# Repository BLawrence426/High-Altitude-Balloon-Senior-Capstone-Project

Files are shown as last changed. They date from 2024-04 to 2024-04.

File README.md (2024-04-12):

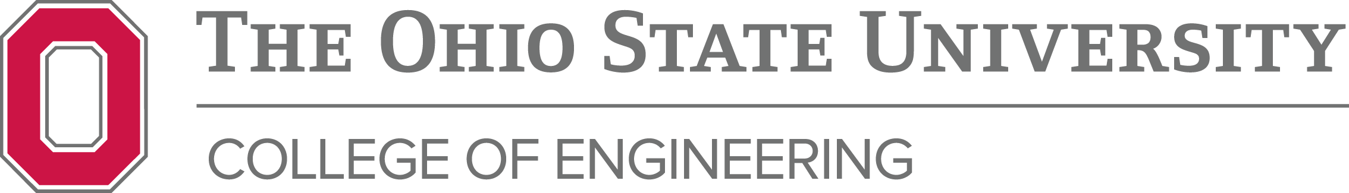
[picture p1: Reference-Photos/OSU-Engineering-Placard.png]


# High Altitude Balloon (HAB) Senior Capstone Project

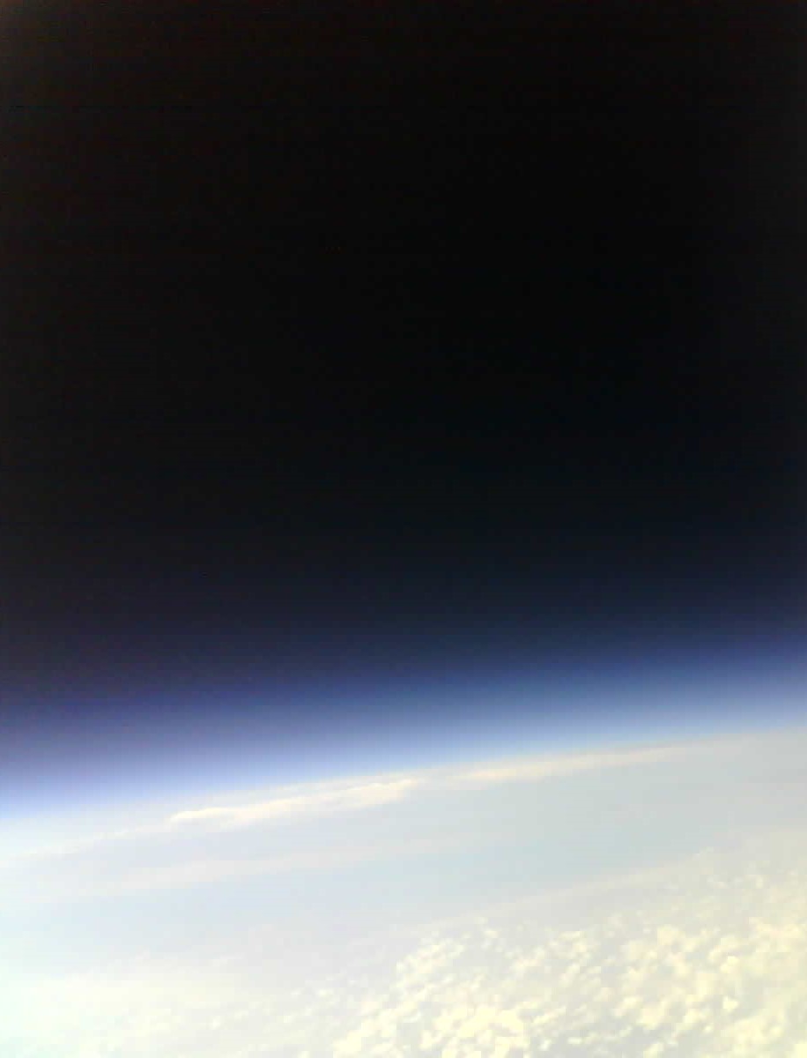
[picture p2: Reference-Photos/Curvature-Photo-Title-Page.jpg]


## Contents
1. [Project Importance](#user-content-project-importance)
2. [Every Parts List](#user-content-every-parts-list)
3. [Payload Construction](#user-content-payload-construction)
4. [Payload Arduino Code](#user-content-payload-arduino-code)
5. [Tracking Receiver Construction](#user-content-tracking-receiver-construction)
6. [Tracking Receiver Arduino and MATLAB Code](#user-content-tracking-receiver-arduino-and-matlab-code)
7. [Launch Protocol](#user-content-launch-protocol)
8. [Launch Experience and Data Results](#user-content-launch-experience-and-data-results)
9. [Flight Test Data Comparison to Simulation Code](#user-content-flight-test-data-comparison-to-simulation-code)
10. [Photo Results](#user-content-photo-results)
11. [Suggestions for Improvements](#user-content-suggestions-for-improvements)
12. [Final Thoughts and Reflection](#user-content-final-thoughts-and-reflection)
13. [Useful Online Tools](#user-content-useful-online-tools)
14. [Resources and Inspirations](#user-content-resources-and-inspirations)
15. [Acknowledgements](#user-content-acknowledgements)

## Project Importance
For my senior year of college at The Ohio State University, we were assigned a capstone group tasked with completing a year-long project. There were a variety of topics we could possibly be assigned; from creating a workbench meant for Starlab to conducting research for both the Navy and Airforce to creating a cost-effective high-altitude balloon (HAB) using off-the-shelf components. Can you guess which one I was assigned?

For more context on the reason behind this project, the first aerospace engineering course (AERO 2200: Introduction to Aerospace Engineering) that each new, bright-eyed sophmore in the major takes will conduct a high-altitude balloon lab at one point. This lab involves a launch of a high-altitude balloon by the professor and other academic faculty in order to collect atmospheric data such as ambient temperature and pressure in order to be analyzed by the students. The purpose for this lab is to teach the students the standard atmosphere (specifically, how air pressure, temperature, and density changes with altitude).

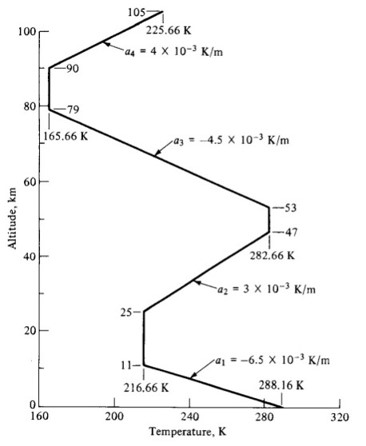
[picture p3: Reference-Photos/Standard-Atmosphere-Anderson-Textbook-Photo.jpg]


#### (Figure from Introduction to Flight Ninth edition by J.D. Anderson, Jr. and M.L. Bowden)

In prior years, including my sophmore year, there were a multitude of issues with the commerical weather balloons that can be bought off the internet (i.e., QRP Light Tracker and Tracksoar). The issues ranging from the balloons themself pre-maturely bursting before it could reach the target altitude or the payload electronics being lost mid-flight. This was a concern to the Mechanical and Aerospace Engineering (MAE) Department since each year they would have to spend upwards of $1000+ for a new weather balloon. This is where our project's importance came in since the goal was to create a new weather balloon payload using off-the-shelf components that was cost-effective (sub $600 for the payload) that could reliably reach a target altitude of 100,000 ft and be recovered for future use. If it couldn't be recovered, the low cost for each payload was important so the department wouldn't need to spend as much money for each launch.

## Every Parts List

### Electronics Parts List

|Hardware|Description|Price|Amount|Total Cost|
| --- | --- | --- | --- | --- |
| [Arduino MKR WAN 1310](https://store-usa.arduino.cc/products/arduino-mkr-wan-1310?selectedStore=us) | The Microcontroller that ran all the payload sensors. Also has built-in Long Range (LoRa) Wide-Area-Network (WAN) module. | $46.00 | 2 | $92.00 |
| [Arduino GPS Shield](https://store-usa.arduino.cc/products/arduino-mkr-gps-shield) | Arduino's own GPS board that can be easily attached to Arduino MKR WAN 1310 board. | $40.10 | 1 | $40.10 |
| [DS18B20 Waterproof Temp. Sensors](https://www.amazon.com/dp/B08V93CTM2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) | Waterproof temperature sensors capable of recording down -55℃. Preferably want two: one for atmospheric temp. and the other for payload internal temp. | $13.48 | 1 | $13.48 |
| [Adafruit MPRLS Ported Pressure Sensor](https://www.adafruit.com/product/3965) | Pressure sensor capable of reading down to 0 psi. Ported end allows for silicone tube to be connected and allow pressure sensor to remain inside the payload | $29.95 | 1 | $29.95 |
| [Adafruit PCF8523 Real Time Clock (RTC) Board](https://www.adafruit.com/product/3295) | Keeps date and time. This helps timestamp each data set for easier analysis of data later. You would think a $40+ Arduino board could do this on its own but NOPE! | $6.95 | 1 | $6.95 |
| [3.7v 3700mAh Lithium Polymer Battery](https://www.amazon.com/EEMB-3700mAh-Rechargeable-Connector-Certified/dp/B08215B4KK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) | Power supply for the entire payload. This may be overkill and can easily be substituted for different capacity battery | $16.99 | 1 | $16.99 |
| [ESP32-CAM Board w/ OV2640 2MP Camera Module](https://www.amazon.com/ESP32-CAM-MB-Aideepen-ESP32-CAM-Bluetooth-Arduino/dp/B0948ZFTQZ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) | On-board camera meant to take photoes every 30 seconds and store to an on-board micro-SD card. This can be omitted if pictures aren't desired | $19.99 | 1 | $19.99 |
| [5mm Micro Mini Slide Switch (3 pin/2 position)](https://www.amazon.com/Tnuocke-Vertical-Position-Switches-SS12D10-G5/dp/B099N61GTZ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) | Turns on/off the payload. | $6.95 | 1 | $6.95 |
| [Micro-SD Card Breakout Board](https://www.amazon.com/Integrated-Circuit-Interface-Raspberry-Breakout/dp/B08C4WY2WR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) | For storing each packet of data on-board the payload iteself. This way if the radio packets end up corrupted or garbage this shouldn't be compromised. | $5.99 | 1 | $5.99 |
| [Wire](https://www.amazon.com/TUOFENG-Hookup-Wires-6-Different-Colored/dp/B07TX6BX47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) | For connecting everything together. I'm weird and I really like color coordinating all my wires so I don't blow anything up. Obviously can be omitted from parts if you already have some.  | $14.99 | 1 | $14.99 |
| [Solder](https://www.amazon.com/Rosin-Solder-Electrical-Soldering-JWOWO/dp/B0C7KZF11F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) | For connecting everything together. I highly, HIGHLY recommend soldering everything together. The jetstreams up above can get pretty nasty and really put your payload through the wringer. | $7.99 | 1 | $7.99 |
| [SUSB Type-C Charging Module](https://www.amazon.com/Charging-Lithium-Battery-Charger-Protection/dp/B08X6G26Q8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) | I noticed some issues with connecting the battery & switch directly to the battery connecter on the Arduino. So I attached one of these to the batteries to make sure it would be fully charged before the flight. | $7.99 | 1 | $7.99 |
| [0.96 Inch OLED Display](https://www.amazon.com/GeeekPi-SSD1306-Display-Arduino-Raspberry/dp/B0833PF7ML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) | Used on the tracking receiver to display the HAB's current latitude, longitude, and altitude. | $14.99 | 1 | $14.99 |
| [1.2" x 1.2" Perfboard](https://www.amazon.com/gp/product/B0CBPRBRTT/ref=ppx_yo_dt_b_search_asin_title?ie=UTF8&psc=1) | Used these to create "hubs" for the various wires. Like connecting all power, ground, SCL, and SDA pins together | $7.09 | 1 | $7.09 |

### Launch Equipment List

|Equipment|Description|Price|Amount|Total Cost|
| --- | --- | --- | --- | --- |
| [Helium](https://www.ballooniacs.com/medium-110-cu-ft-helium-tank-rental/) | Obviously need helium for our balloon. Tank rentals can vary, but if you are in the Columbus, OH area I highly recommend BALLOONIACS. They are very nice and were able to get us a tank of helium on very short notice. Just make sure you double check how much helium you will need before launch! | ~$300.00 | 1 | ~$300.00 |
| [Balloon(s)](https://www.scientificsales.com/8244-Weather-Balloon-1200-Grams-Natural-p/8244.htm) | Obviously need a balloon so our project lifts of the ground. Just double check the size balloon you need to reach your target altitude. We went with a 1200 gram balloon in order to reach 100,000 ft | $110.00 | 1 | $110.00 |
| [Pressure Regulator](https://www.amazon.com/Harris-3000606-25GX-Regulator-500-580/dp/B005V0RAYI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) | A pressure regulator helps fill the balloon safely. This is similar to the one we used, I just recommend getting one with a flared end in order to screw directly into the helium bottle. Obviously this can be replace with a similar device/method that is cheaper or more accessible to you! I was just fortunate enough to borrow one from our engineering department | $141.07 | 1 | $141.07 |
| [Quick Disconnect Hose](https://www.amazon.com/Hromee-Compressor-Fittings-Industrial-Coupler/dp/B08V17V6WJ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) | Air compressor hose for connecting the helium bottle to our ball-valve nozzle that is used to fill the balloon (pictured below). Doesn't have to be this exact same one, I just suggest something similar to this one. | $19.99 | 1 | $19.99 |
| [Fish Scale](https://www.amazon.com/dp/B07JWGHC48?ref=ppx_yo2ov_dt_b_product_details&th=1) | You can use this to determine how much helium is in your balloon. This gives the buoyancy force and then you can figure out the volume of helium inside the balloon if you assume it's spherical. I suggest making sure the fish scale can read the intended buoyancy force. | $19.99 | 1 | $19.99 |
| [Teflon Tape](https://www.menards.com/main/plumbing/plumbing-installation-repair/pipe-sealants-caulk-putty/blue-monster-teflon-pipe-thread-sealant-tape/70886/p-1444440440571-c-853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) | For sealing the threads of the pressure regulator when screwing it into the helium bottle | $4.31 | 1 | $4.31 |
| [Large Zip Ties](https://www.walmart.com/ip/Hyper-Tough-14-5-inch-75lb-Yellow-Cable-Ties-50-Count/595201774?from=/search) | For sealing the balloon and attaching the payload/parachute to the balloon. I recommend wrapping the part of the zip tie that will rub up against the balloon with a bit of electrical tape in order to prevent it from cutting the latex | $7.48 | 1 | $7.48 |
| [Wrenches](https://www.menards.com/main/tools/hand-tools/pliers-plier-sets/masterforce-reg-groove-joint-pliers/84-550/p-1444425505984-c-9156.htm) | For screwing the pressure regulator into the helium bottle. Just make sure whichever ones you use will fit the nut on the pressure regulator you're using | $9.78 | 1 | $19.78 |
| [Tarp](https://www.walmart.com/ip/Hyper-Tough-Weather-Resistant-Light-Duty-6-x-8-Polyethylene-Tarp/603949195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) | For setting up the balloon. Un-rolling the balloon in the grass can cause issues with the latex so I highly recommend getting a big tarp to set everything up | $4.66 | 1 | $4.66 |
| [Ball-Valve Filling Apparatus](https://www.highaltitudescience.com/products/3-cm-max-safe-inflator) | Mentioned previously, this was inserted into the neck of the balloon in order to fill it. A picture of it is included directly below. I HIGHLY reccommend you making your own. A hundred dollars for this one seems a bit extreme in my opinion and you could definitely make one for cheaper. | $99.99 | 1 | $99.99 |

### Personal Protective Equipment (PPE) List
|Equipment|Description|Price|Amount|Total Cost|
| --- | --- | --- | --- | --- |
| [Safety Glasses](https://www.amazon.com/dp/B016KZ2APQ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) | Want to be safe and protect your eyes! | $18.16 | 1 | $18.16 |
| [Vinyl Gloves](https://www.amazon.com/Schneider-Latex-Free-Powder-Free-Disposable-Examination/dp/B09KRSXZNL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) | The oils in your hands can cause week spots to form in the weather balloon so you really want to wear gloves when handling it. Just make sure they fit your hand size! | $7.57 | 1 | $7.57 |

### Payload Equipment List
|Equipment|Description|Price|Amount|Total Cost|
| --- | --- | --- | --- | --- |
| [Payload Chassis](https://www.amazon.com/HATCHBOX-3D-Filament-Dimensional-Accuracy/dp/B00J0ECR5I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) | Of my own design. It used a little under half a spool of PLA filament. I linked my preferred filament brand but use what ever your heart desires! | $24.99 | 1 | $24.99 |
| [1/2 Inch Syrofoam Insulation Board](https://www.homedepot.com/p/Owens-Corning-FOAMULAR-NGX-Insulating-Sheathing-0-5-in-x-4-ft-x-8-ft-SE-R-3-XPS-Rigid-Foam-Board-Insulation-13NGX/315193939) | Used this to make a shell to go on the outside of the chassis. This is to keep everything nice and toasty | $13.98 | 1 | $13.98 |
| [Aluminum Tape](https://www.amazon.com/Aluminum-Ductwork-Temperature-Insulation-Adhesive/dp/B0B6NDFXPN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) | Used this to assemble and seal the styrofoam shell. Doesn't need to be airtight nor should it be (though a very slim chance, could de-pressurize and explode). | $5.99 | 1 | $5.99 |
| [Bubble Wrap](https://www.walmart.com/ip/Duck-Max-Strength-Large-Bubble-Cushioning-Wrap-12-in-x-100-ft-Clear-287223/46582773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) | Wrapped the entire payload in bubble wrap for extra cushion upon impact. I was a bit worried about the impact velocity so I did this for ease of mind | $19.48 | 1 | $19.48 |
| [Plastic Paper Sheet Protector](https://www.walmart.com/ip/Pen-Gear-Economy-Sheet-Protectors-20-Sheets-Clear-8-5-x-11-Model-25038/935038091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) | This is for protecting the little placard I made with my contact information | $1.18 | 1 | $1.18 |
| [Packing Tape](https://www.walmart.com/ip/Scotch-Heavy-Duty-Shipping-Packing-Tape-Clear-1-88-in-x-25-6-yd-1-Tape-Roll-with-Dispenser/438482605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) | Used this for attaching the bubble wrap to the styrofoam shell | $3.58 | 1 | $3.58 |
| [Handwarmers](https://www.walmart.com/ip/HotHands-Hand-Warmer-10-Pair-Value-Pack/17808715?wl13=3792&selectedSellerId=0) | Heating source for the payload electronics | $7.48 | 1 | $7.48 |
| [Parachute](https://the-rocketman.com/recovery-html/) | Used for slowing down the payload upon the descent. I suggest weighing your payload and adding on the weight of the balloon youre using then going to the rocketman website to see what parachute size is suitable. I went with a 3ft parachute but I think we should have went up to either a 4ft or a 5ft parachute to slow it down even more. | $45.50 | 1 | $45.50 |
| [Paracord](https://www.walmart.com/ip/Hyper-Tough-550-Utility-Paracord-Rope-Orange-5-32-inch-x-50-feet/459593415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) | Used this for attaching the bubble wrap to the styrofoam shell | $4.84 | 1 | $4.84 |
| [Tape Measure](https://www.menards.com/main/tools/hand-tools/measuring-layout-tools/tape-measures-rulers/masterforce-reg-force-blade-trade-tape-measures/m52416/p-1460081133564-c-15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) | Used for measuring the length of the paracord between the payload/parachute/balloon | $7.09 | 1 | $7.09 |

### Miscellaneous Equipment List
|Equipment|Description|Price|Amount|Total Cost|
| --- | --- | --- | --- | --- |
| [Scissors](https://www.walmart.com/ip/Scotch-8-inch-Multi-Purpose-Stainless-Steel-Scissors/19675467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) | Used this for cutting bubble wrap and paracord | $3.62 | 1 | $3.62 |
| [Side Cutters](https://www.menards.com/main/tools/hand-tools/pliers-plier-sets/micro-flush-cutter/cwcmf/p-1444421187059-c-9156.htm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) | Used this for cutting paracord and zip ties | $3.55 | 1 | $3.55 |
| [Small Zip Ties](https://www.walmart.com/ip/Hyper-Tough-4inch-Cable-Tie-Uv-Black-100Pcs/440215826?athbdg=L1102&from=/search) | Used these for, albeit rough, cable management of thepayload electronics | $3.22 | 1 | $3.22 |
| [Electrical Tape](https://www.walmart.com/ip/Hyper-Tough-50ft-Vinyl-Electrical-Tape-3-4-0-43lbs-Black-3-Pack-34366/191038268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) | Used this for wire insulation and wrapping the PVC pipe used in the filling valve | $2.13 | 1 | $2.13 |
| [Lighter](https://www.walmart.com/ip/Ozark-Trail-Multipurpose-BBQ-Lighter-Red-and-Black-2-Pack/1450295214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) | Used for melting the cut ends of paracord so they don't keep fraying and coming loose | $2.24 | 1 | $2.24 |
| [Heat Shrink Tubing](https://www.amazon.com/Shrink-Tubing-Tubes-KOOWIN-Ratio/dp/B098LB9LTJ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) | The payload electronics are packed pretty tightly so I figured it would be best to insulate everything as neat as possible. This is the kit I used, but use whatever you feel like doing! | $7.99 | 1 | $7.99 |

## Payload Construction

When designing our HAB payload, the biggest fear that we needed to resolve was the absolute beating our payload electronics were expected to endure during a test flight. The jetstreams up above can get pretty nasty, so making sure that every component was a) soldered together and b) held down in some fashion was important to ensuring nothing would come loose and possibly short out the entire payload electronic system. Likewise, we wanted our payload to remain light (Under 2 pounds total, but preferably less) for safety reasons. So in conclusion, these three main considerations is what drove our design for what we are calling our payload chassis:

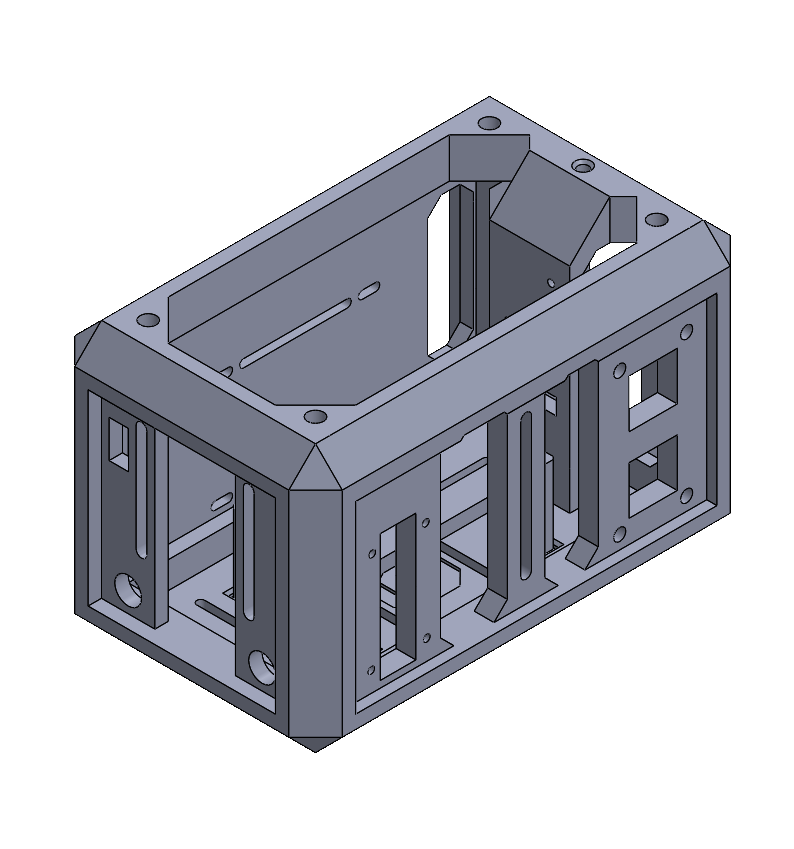
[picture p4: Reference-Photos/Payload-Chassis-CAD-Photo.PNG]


The chassis ended up having dimensions of 400x400x600mm (Base x Height x Width) and was 3D printed on my Ender 3 Pro printer using black hatchbox PLA. Chamfers were placed in as many locations as possible in order to cut-down on support material and decrease the printing time. Likewise, 10% infill was used but with 4 walls in order to help with strength and rigidity. This chassis is also divided up into two seperate pieces: the shell itself and a little platform with legs that was used for holding the Arduino MKR WAN 1310 board while still allowing for wires to pass underneath and be soldered to its pins. For more images of the chassis CAD files as well as the Solidworks files themself, go to the [Payload CAD Files](Payload-Chassis-CAD-Folder) folder up above!

Though its hard to see, I tried my best to remove as much unecessary material as possible while also providing ample mounting locations for each and every one of our electronics. The little holes seen all around our payload chassis are locations to melt threaded brass inserts into which provide locations that each part can be screwed down into. Similarly, I also tried putting a bunch of slots all around the chassis so zip ties could be passed through in order to hold everything into place. Our final designed had the Arduino MKR WAN 1310, micro-SD card board, RTC board, pressure sensor, and small perf boards screwed down and the wires, battery cell, antenna, and handwarmer zip tied to the chassis. The only odd methods out for mounting components onto our payload chassis were the ESP32-CAM board and the GPS shield. The GPS shield was insertted onto the top of the Arduino MKR WAN 1310 board and then hot-glued down to keep it from coming apart or shifting during flight. And then the camera was insertted into its own clam-shell case that was epoxied into a dedicated space on the chassis. This [clamshell case](https://www.thingiverse.com/thing:4251986) was designed by the username dandesc on Thingiverse.com and I decided to adapt it to work with our project. I belived this was a quicker way to provide a dedicated space for the camera to mount to while also making replacing it in the future if needed easy as well. And then once the chassis parts were printed, post-processed, and fully assembled I was left with this:

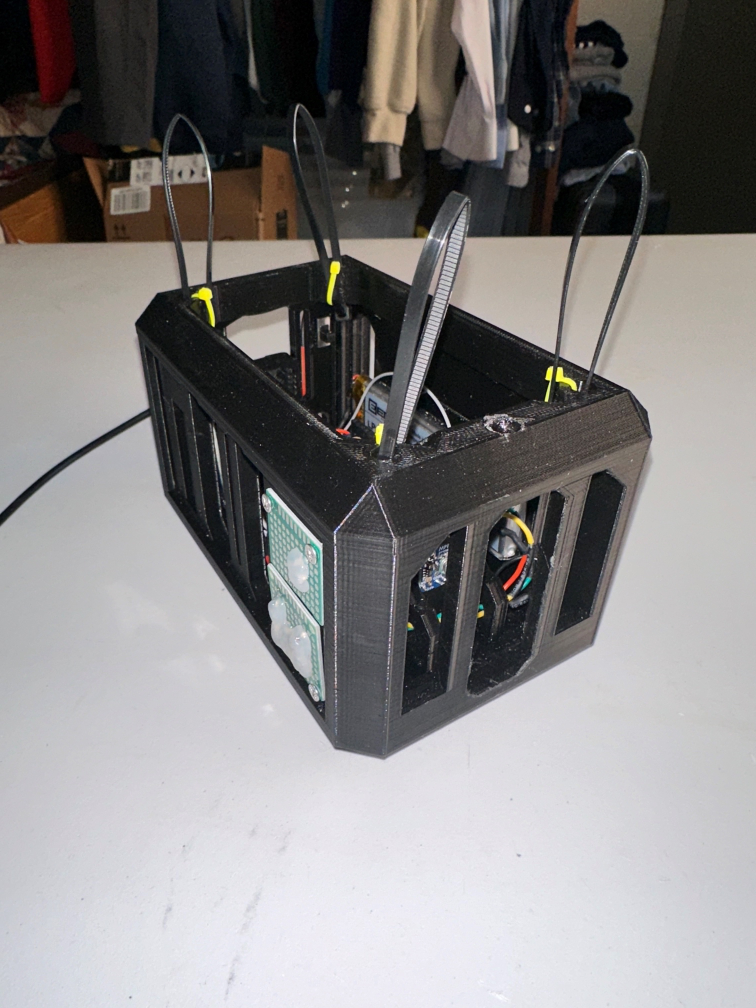
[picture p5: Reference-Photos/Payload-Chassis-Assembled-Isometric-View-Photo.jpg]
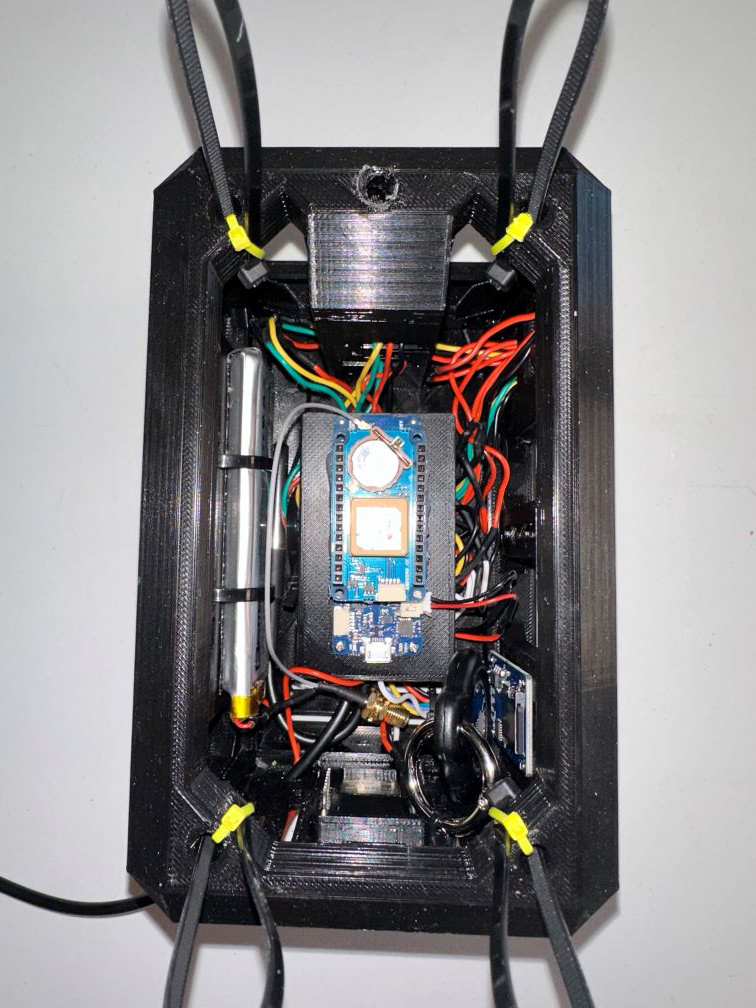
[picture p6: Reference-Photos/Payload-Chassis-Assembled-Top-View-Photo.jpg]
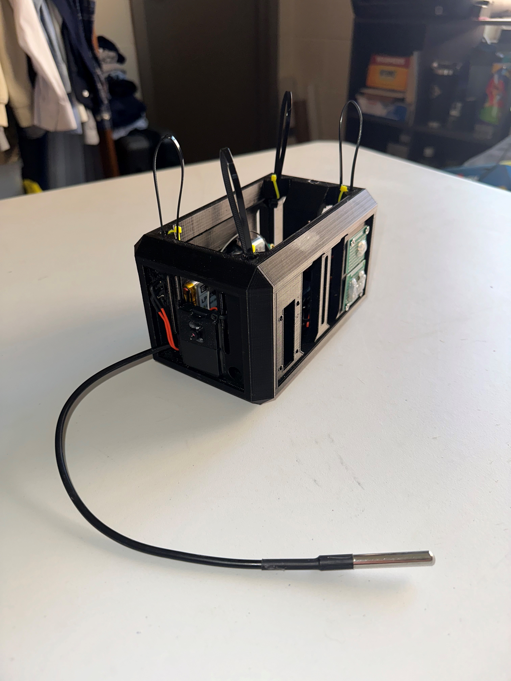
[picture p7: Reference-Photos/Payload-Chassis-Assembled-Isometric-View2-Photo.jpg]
  

My mindset for going this route instead of just saying screw it and epoxying all the components down was due to my desire to make each component easily replaceable if need be. I figure at some point a sensor or component will be damaged upon impact, so I figured I would try my best to future proof our mounting methods for each component. Plust it helped me with debugging things when I was assembling it all together and needed to address a weak connection to a component.

Likewise, when desinging our HAB payload, we did extensive online research and found a variety of individuals who posted their own HAB payload designs. The one design decision that was seen in all the ones we found was the use of an outer-styrofoam shell. These shells ranged from using small, disposable styrofoam coolers to even floral arrangement foam that was hallowed out. We decided to go a slightly different route and use 1/2 inch rigid foam insulation board and create an outer shell of this material that would go around our 3D printed chassis. A picture of our final styrofoam shell can be seen below:

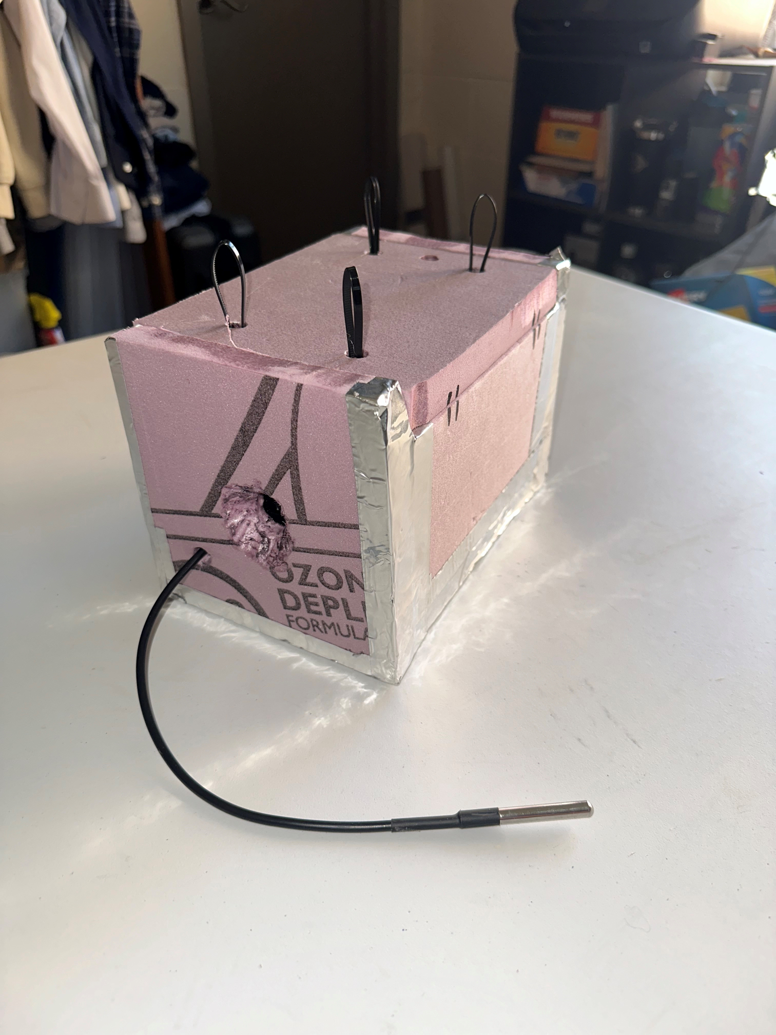
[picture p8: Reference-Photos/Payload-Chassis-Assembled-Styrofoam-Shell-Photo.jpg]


And then just to give us a bit more ease of mind with our payload, we decided to wrap it in several layers of bubble wrap in order to help cushion the impact force just incase our payload would happen to hit someone or their property.

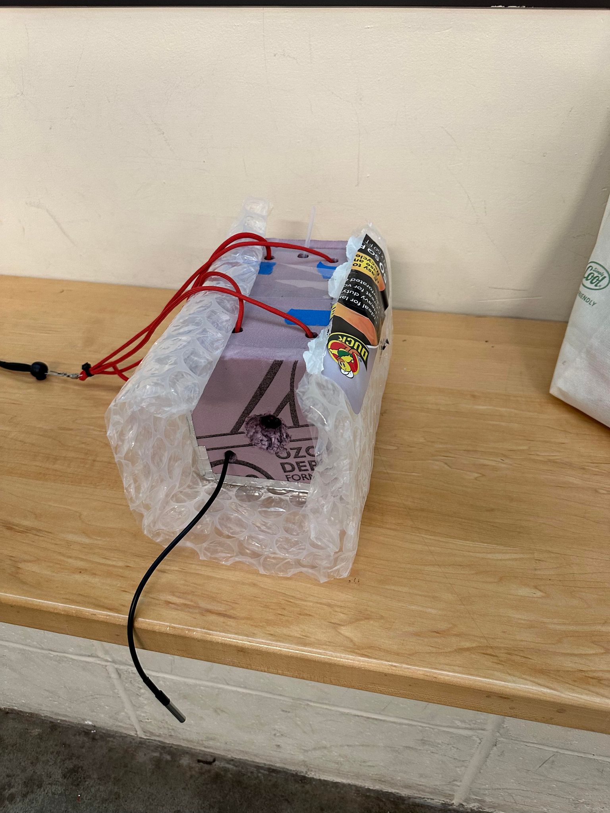
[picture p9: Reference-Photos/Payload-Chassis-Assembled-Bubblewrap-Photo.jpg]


## Payload Arduino Code

Disclaimer, but this was my first big project that utilized Arduino and the coding language so I apologize upfront if my code looks terrible. I know it's not as optimized as it could be, but I made sure to comment it as best as possible so everyone can follow it. Below I'll try to explain what the code does:

Firstly, the [Payload Arduino Code](Payload-Arduino-Code-Folder) is broken up into two files: the main arduino code and the camera code. The main arduino code is what gets the current interior payload temperature, exterior ambient temperature, ambient pressure, GPS data (latitude and longitude), and date/time and both saves the data to the backup micro-SD card and transmit packets of data via the on-board LoRa WAN module in .csv format. I also included two versions of the main arduino code which either use 915 MHz or 433 MHz for transmitting its data packets depending on what you prefer. Furthermore, this code also communicates with the ESP32-CAM and tells it when to take a photo (every 30 seconds). So then on the flipside, the camera code waits until it receives a trigger from the main arduino board that tells it to take a photo. 

The reason for the odd way of integrating the ESP32-CAM to communicate with the Arduino MKR WAN 1310 board was simply due to my novice understanding of this coding langauge and overall frustration with getting this code to work. The original plan was to use an [Arducam OV2640](https://www.amazon.com/Arducam-Module-Megapixels-Arduino-Mega2560/dp/B012UXNDOY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) since that can be easily integrated into the main arduino code. However, I ran into issues where the photos from the Arducam OV2640 were either blurry, green/magenta tinted, or just completely dark. I did extensive research over a week of trying to trouble shoot this issue and believe this issue was caused by the lack of on-board ram for processing and saving the photos to a micro-SD card. I'm sure there lays a solution that allows for this camera to work with the main arduino board for this application, however I'll be completely honest and admit that finding that solution is way over my head. I would love to hear if anyone else was able to get an Arducam OV2640 to work with an Arduino MKR WAN 1310 board and return decent photographs and learn how they did it.

My solution to this problem, however, was found when I stumbled upon the ESP32-CAM boards which are essentially arduino boards with the same camera as the Arducam OV2640 board along with ample ram and its own micro-SD card board that it can save to. I ended up setting up the ESP32-CAM to wait for a pulse sent to its GPIO 1 pin by the main arduino board. Once a pulse was received, then the ESP32-CAM knew to take a photo and save it to its own micro-SD card.

It should be noted that the main arduino code doesn't run correctly unless the following conditions are met:
  - It can find both the interior and exterior temperature sensors
  - It can find the pressure sensor
  - It has a GPS signal (it will stop transmitting/saving data if its GPS signal is lost and will pick back up once fixed)
  - A micro-SD card used for saving the backup data is insertted/found
  - It can find the Real Time Clock (RTC) Board
  - The LoRa WAN modue is found
    
Below is a flow chart to try and help you visualize how the code operates:

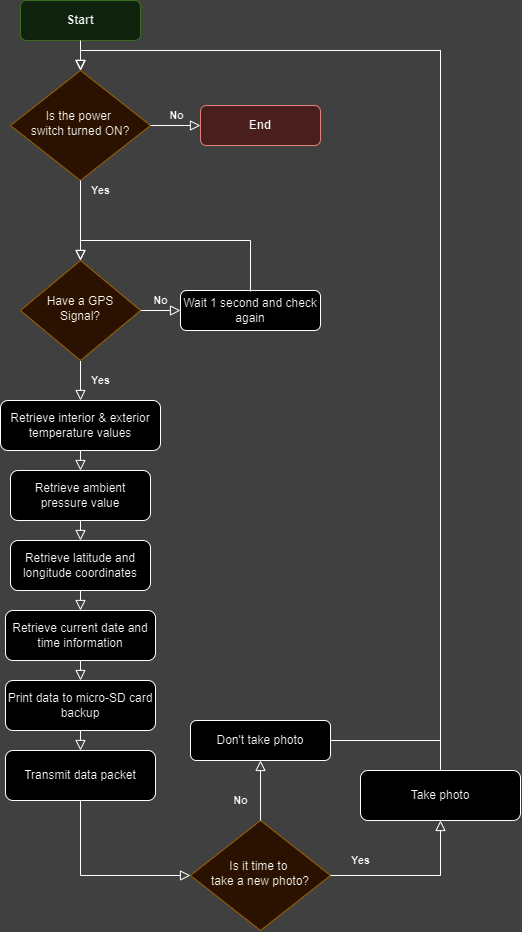
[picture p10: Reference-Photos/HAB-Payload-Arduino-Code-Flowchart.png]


And then to help you visualize roughly how each component was soldered together, I made the following schematic for our presentation and figure I would include it here. Just to make a small note that the schematic doesn't show, I ended up using two small pieces of perfboard to create a sort of 'hub' for each component that needed to share a specific wire to connect to. In other words, the components that needed a ground, 3.3V, Serial Clock Line (SCL), and Serial Data Line (SDA) wire were all connected to these perfboard 'hubs'. These connections were all done on a single piece of perfboard, with a second piece being used in order to connect the 3.3V to 5V converter board. During testing, I found that the Arduino couldn't recognize the micro-SD card nor board when everything was running off of 3.3V and when I tried using 5V on a whim everything worked flawlessly. Depending on what micro-SD board, this may not be an issue for you but if it is I suggest saving yourself a possible headache and try this to see if it works!

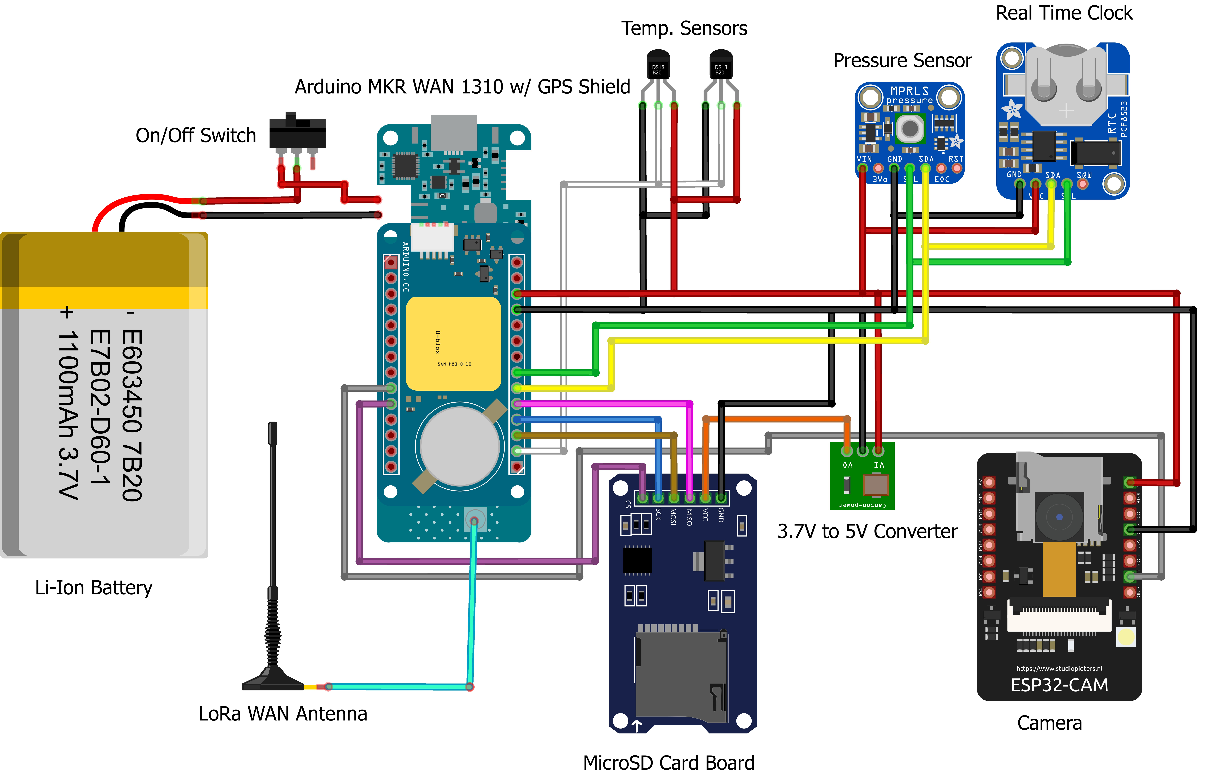
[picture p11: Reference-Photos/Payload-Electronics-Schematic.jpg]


Here is the list of each wire color shown in the schematic and what their purposes are:
1. Red: 3.3v
2. Black: Ground
3. Orange: 5v
4. White: Temperature Sensor Communication
5. Green: Serial Clock Line (SCL)
6. Yellow: Serial Data Line (SCA)
7. Purple: Micro-SD Card Board Communication
8. Pink: Master-In, Slave-Out (MISO)
9. Brown: Master-Out, Slave-In (MOSI)
10. Blue: Serial Clock (SCK)
11. Gray: Camera Communication
12. Cyan: Antenna

## Tracking Receiver Construction

The tracking receiver was constructed in a similar manner to the payload chassis described above. It was 3D printed and utilized threaded brass inserts in order to mount the necessary electronics for it to function. The receiver shouldn't experience any necessary forces (unless I drop it) but I just soldered them all together out of habit. Below is a picture of the CAD file:

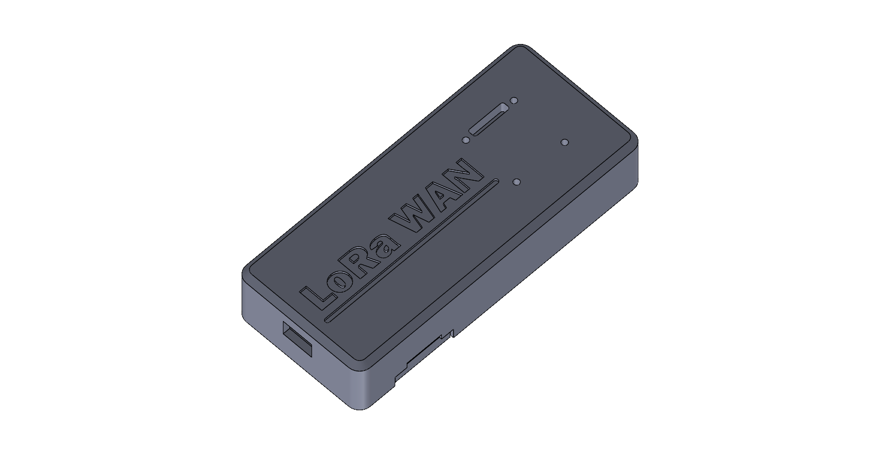
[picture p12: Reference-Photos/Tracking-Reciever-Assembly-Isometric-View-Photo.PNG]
 

And then here is a picture of the fully assembled tracking reciever. It can be hand-held like I did in the photo, but also attached to a laptop and used in tandem with a MATLAB script I also wrote. This way of using the tracking reciever is outlined more in the next section, but here is a photo of how the tracking reciever looked when fully assembled:

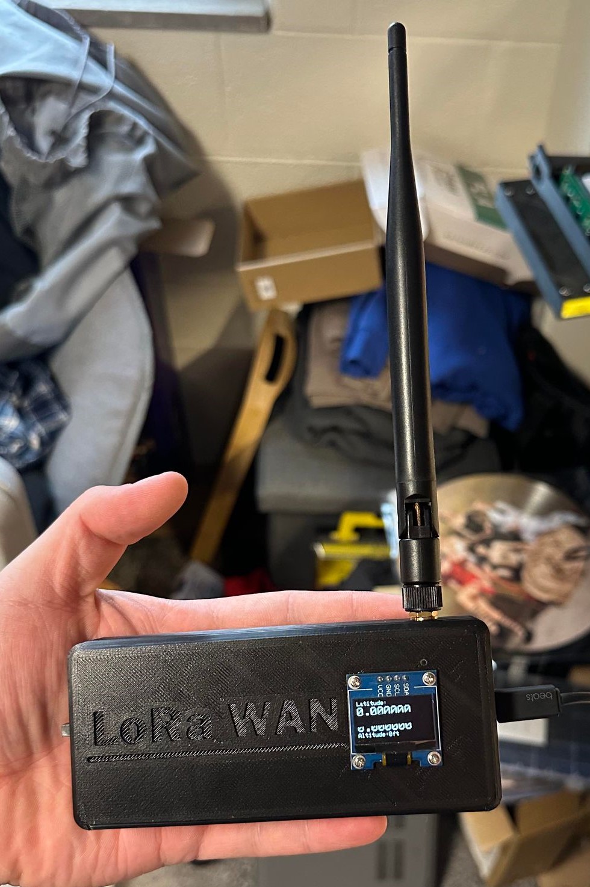
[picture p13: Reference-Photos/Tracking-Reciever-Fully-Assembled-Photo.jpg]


This tracking receiver had a kill switch on the side, a micro-SD card board for saving the packets of data just in case, and a coaxial connection out the top for an antenna to be connected to. For this project, I purchased a magentic antenna base that I attached attached to the top of my car so I could drive and track the balloon mid-flight:

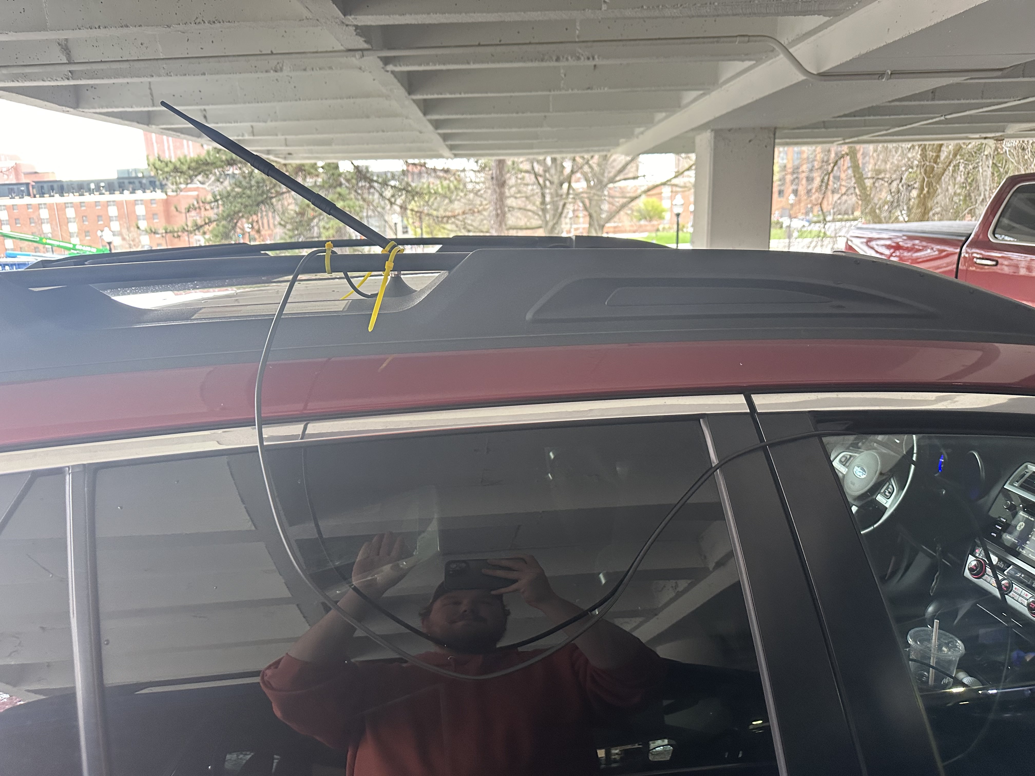
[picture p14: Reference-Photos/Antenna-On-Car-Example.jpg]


I did zip-tie it to my luggage rack on the roof of my car just in case if it would've fallen off while driving, but it doesn't seem to have moved at all which was good!

## Tracking Receiver Arduino and MATLAB Code

Similarly to the payload code, the tracking receiver code works in two parts: another Arduino MKR WAN 1310 that is meant to intercept the packets being sent back to the ground by the HAB payload along with a MATLAB script that takes the packets of data and parses out the latitude and longitude coordinates in order to live-plot them on a geoplot.

The arduino code itself is pretty simple; it just waits until it receives a packt of data like mentioned above. And once one is received, it then parses out the data and sends it the MATLAB script as well as prints it to a mini OLED screen on the receiver itself. This way, it can also be used in a hand-held mode in conjunction to the MATLAB tracking code.

The [MATLAB code](Tracking-Reciever-MATLAB-Code-Folder) turned out to be simpler to create than I originally anticipated. It also takes in the packets of data, still in .csv format, and parses out each variable (interior temperature, exterior temperature, ambient pressure, latitude, longitude, altitude, and # of satellites). Then it specifically takes the latitude and longitude coordinates and plots them onto a geoplot. The plan for this was to have someone in the passenger seat of my car with a laptop and both the receiver code and MATLAB plotting code running. This way I could drive while they relay information was to where the balloon is drifting off to.

So to talk about how this worked in practice, I can sum it up in one simple word: terribly. After we launched the balloon and packed everyting back up in my car, we immediately drove after it with the receiver running on my computer and the antenna on top of my car. It worked for a bit, but once we got onto the highway we didn't get another packet of data. We kept driving hoping we would get more as we continued in the direction it was heading, but nothing. After we went a while without another packet, we decided to drive out where we estimated it to land in order to get a signal when it was coming back to Earth, but we still got nothing. And after driving around for 7 hours with no new packets of data, we called it quits and considered it lost.

## Launch Protocol

Never having launched a high-altiude balloon before, it honestly wasn't as bad as I initially expected. There are plenty of videos out there, the two I found most informative was one by [StratoStar](https://www.youtube.com/watch?v=5Z23L4QIgtQ&ab_channel=StratoStar-JasonKrueger) that walked you through the basics of filling the balloon and another one by [John Powell](https://www.youtube.com/watch?v=B7XEUJSekbI&ab_channel=JohnPowell) that walked you through rigging our payload to the balloon. Both of these videos had some really good, basic points that made filling the balloon seem very simple to a novice such as myself. Though I urge you to do your own research until you feel comfortable; there are plenty of amazing, informative videos on this topic and you can really get a good idea of what you're doing without ever attempting something like this beforehand.

So with those informative videos mentioned, I feel that it is helpful to talk about our criteria for what a good day to launched looked like. These were our parameters that we were on the look for in terms of weather:
  - A ground temperature above 40°F
  - Daylight (between sunrise and sunset)
  - Max windspeed of 15 mph
  - Visibility of 5-10 nautical miles
  - Little to no precipitation/Incliment Weather
  - Little to no Cloud Cover (Important to us since we included a camera with our payload)

Now you all can decide what conditions you would prefer to launch in; such as wanting less wind, not worrying about ground temperature as much, and not caring for cloud cover if youre not including a camera on-board. The sky's the limit (pun intended) for your launch, just make sure you are being safe about it and not like launching the balloon at night with no light-strobe included!

Then, after watching several videos on high-altitude balloon launches and coming up with our list of criteria for optimal launch conditions, we devised a set of instructions for us to follow in order to have a quick, accident free launch:
  1. Prior to launch, check the weather forcast daily the week leading up to the intended launch date
  2. Ensure the payload, parachute, and paracord rigging lines are completely assembled beforehand to make it simple to attach to the balloon
  3. Drive to launching location. Ensure that the helium bottle is properly secured in the vehcile in order to prevent damage to the bottle
  4. Lay tarp flat on the ground and put bottle and other heavy objects in the corners to prevent it from lifting up
  5. Attach the pressure regulator to the bottle with wrenches. Make sure to put teflon tape on the threads to prevent leaking if the regulator doesn't have a flared end. Also do not open the helium bottle yet
  6. Attach the quick disconnect hose to the pressure regulator along with the ball-valve filling apapratus
  7. Set out rest of supplies needed for filling the balloon so you don't have to go searching for them. These include the fish scale, zip ties, payload with rigging and parachute attached, electrical tape, and either scisors or side cutters
  8. Put on nitrile/latex gloves. These are needed by everyone who may need to touch the balloon
  9. Open the bag that the weather balloon came in and carefully open it and lay it flat onto the tarp. Make sure not to step on it at all
  10. Insert ball-valve filling apparatus into the neck of the balloon carefully in order to prevent tearing of the latex
  11. Attach fish scale to both the helium bottle and the neck of the balloon via paracord and zipties. This will be used to measure buoyance force
  12. Once the ball-valve filling apparatus and fish scale/tether is attached to both the helium bottle and balloon, ensure that the pressure regulator valve is fully closed and then fully open the helium bottle valve
  13. Begin filling the balloon by slowly openning the pressure regulator valve. Once the balloon is off the ground and above the bottle, you may then increase the fill rate
  14. While the balloon is filling, feel free to turn on the payload electronics and the tracking code and get those running.
  15. Once the payload is verified to be on and operating, tape shut the lid for the styrofoam shell and attach the bubble wrap onto the outside of the styrofoam shell
  16. Once the balloon is either filled to the desired buoyancy force or the helium bottle is fully depleted, close the pressure regulator valve.
  17. Attach the parachute and payload to the balloon via paracord and zipties. Its good practice to first twist the neck of the balloon and and then zip tying the payload and parachute to where its twisted. This will help prevent helium leaking.
  18. Remove the ball-valve filing appartus but leave in the PVC fitting. This will help prevent the zip tie from slipping off.
  19. Fold the rest of the neck of the balloon up and zip tie into place, this again is to prevent helium from leaking out and from keeeping the payload from slipping off the balloon mid-flight
  20. Once the payload is fully attached, ball-valve filling apparatus is removed, and the payload electronics and tracking receiver are confirmed to be working correctly, cut the tether line holding the balooon to the helium bottle and watch it drift
  21. Pack up everything into your vehicle and get the tracking receiver and MATLAB code running on a laptop running in the passenger seat. Passenger optional depending on your skill level
  22. Track the balloon and hopefully recover it.
  23. PROFIT!

## Launch Experience and Data Results

We launched our balloon a little bit southwest of Columbus, OH at a AERO RC Club on April 9th, 2024. Launching it went really well in my opinion and only took an hour from parking my car to launching the balloon and packing everything up with the help of our faculty advisor. Here are some of the photos we took of our launch:

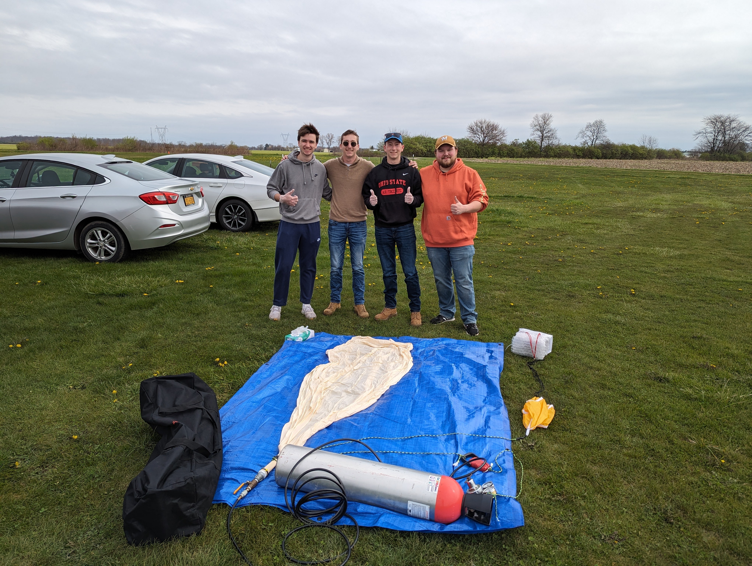
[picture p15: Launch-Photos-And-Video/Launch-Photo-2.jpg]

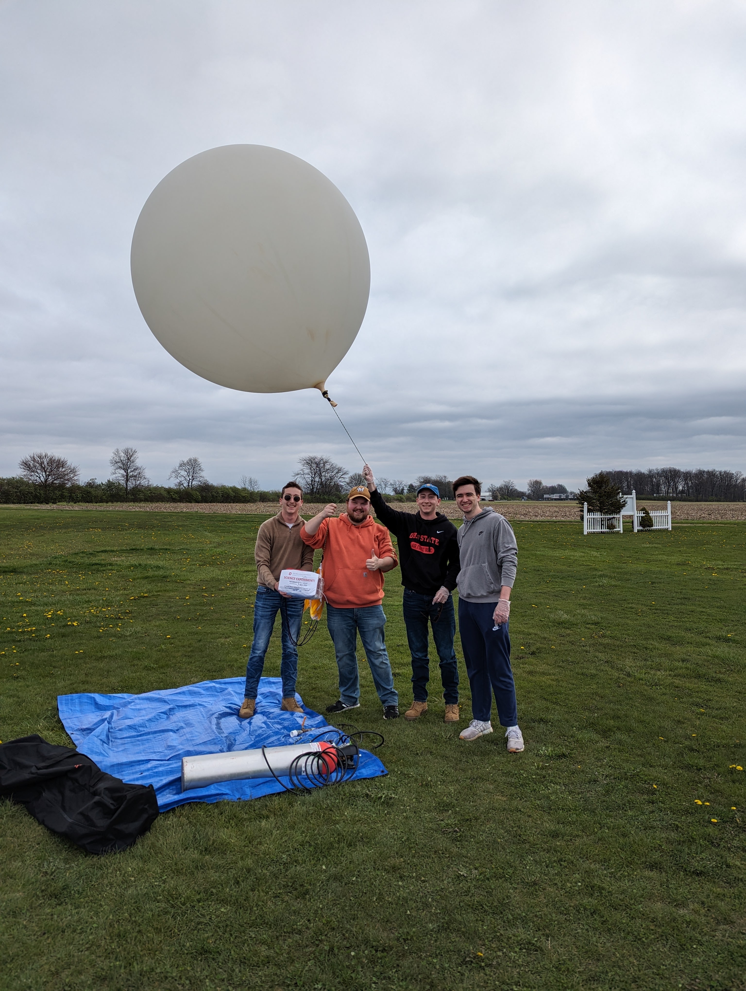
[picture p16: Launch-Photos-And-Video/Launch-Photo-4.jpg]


And so, with a ton of zip ties, electrical tape, paracord, and 110 cubic feet of helium, we were able to get a successful launch:

https://github.com/BLawrence426/High-Altitude-Balloon-Senior-Capstone-Project/assets/157772655/674f84ac-60b6-4e0f-a145-dcf7288c7ae6

Following this video being taken and a couple of more minutes of watching it drift away, we loaded up everything into my car and myself and a member of my team started driving after it. Like I mentioned in the previous section about our tracking receiver, it honestly failed as soon as we got out of Columbus. We immediately jumped onto I-70 which went straight east out of Columbus since that was the direction we were predicting the balloon to drift. We were getting packets of data right when the balloon lifted off and for a short period of driving, but shortly after we got onto the highway we lost contact with the balloon and were now in search and rescue mode. We ended up driving to east near Barnesville, OH, which is roughly where our balloon was predicited to land:

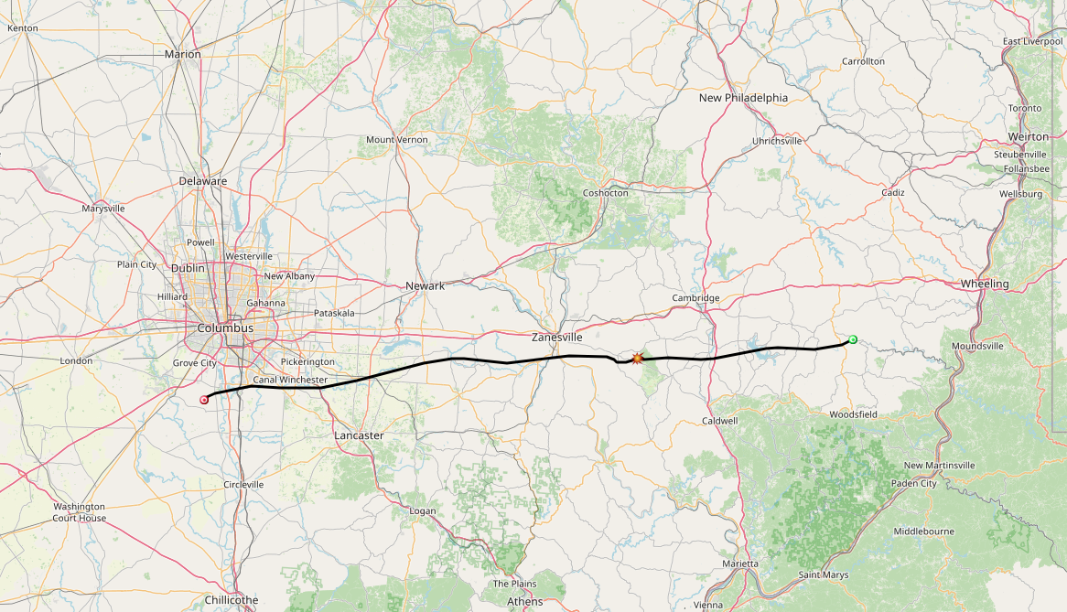
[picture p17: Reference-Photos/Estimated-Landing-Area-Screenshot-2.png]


We got there roughly when it was supposed to land (about 1.5 hours following lift-off) and were scanning the local sky and checking our tracking receiver. After spending about 30 minutes in a remote, hilly farmland we decided to call it quits in that location and started to drive around hoping for a signal to make it to us. We spent an hour driving around a bunch of gravel backroads up and down the hilly terrain of eastern Ohio and came up with nothing. We decided to call it quits looking around this area and took county roads back to Columbus that more closely followed the estimated fightpath in-case the balloon happened to of prematurely burst. In all, we spent 7 hours directly after launching the balloon trying to located it before its battery died but came up short. At this point, we called it a loss which was dissapointing but we knew the risk we were taking.

But this isn't where the story ends!

I happened to purchase and put an Apple Air Tag in with the payload before launch on a whim. My mindset was that if we got close enough to the payload while trying to find it, I figured I could use my phone to play a sound in order to locate it quicker if it was stuck inside a bush or something. I knew that these Air Tags aren't worth their salt when it comes to trying to find something in the middle of nowhere due to them needing to connect to an apple device in order to project its location on the "Find My" App created by Apple. And after returning to The Ohio State's campus and taking a short nap (sorry, I was exhausted) I happened to check the app and saw it actually updated its location!

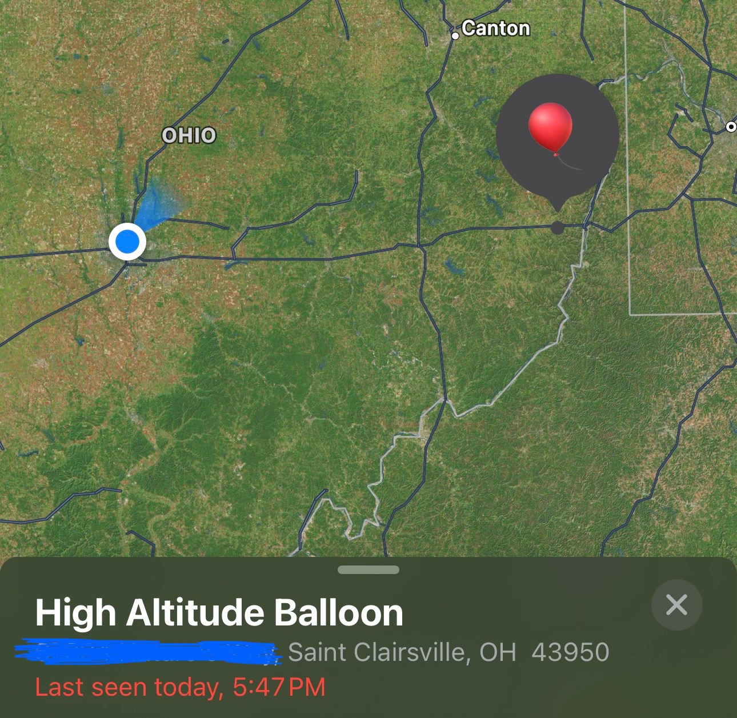
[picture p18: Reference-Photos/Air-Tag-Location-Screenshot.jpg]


It moved!! I was so excited and my hope for trying to find it was off the charts. It followed the predicted path really close, but ended up drifting about 20 more miles eastward than we intended which would explain why we weren't able to either see it descend nor receive a packet of data. And thankfully, it appeared to land in the backyard of a couple of condos that shared a walking path in their backyard which would explain why it was able to connect to an Iphone relatively soon after it landed back onto the ground. So following this new information, I devised a plan to drive back out to eastern Ohio in order to find and recover it without needing to tresspass on anyones property. So following my Flght Testing course, I set off for my 2-hour journy to Saint Clairsville which the Air Tag was showing it was located at.

When I finally arrived I did a quick loop on the road that overlooked the location it was showing to be and I swore I saw the yellow parachute on a bench near the walking path it was located. So then I eventually turned around in someones driveway and went down the road that the duplexes with the backyards in which our balloon payload was located in. I was extremely lucky that there were a couple of landscapers out tending to the grass and mulch beds that were kind enough to help me try and find it (I hope they enjoyed a beer or two on me from the card I left on their truck!). Myself and the first landscaper I talked to had a nice conversation while walking towards a bench alongside the walking path the Air Tag was showing its location at and, sure enough, someone happened to come across the payload and leave it on the bench. Though a bit wet from a thunderstorm that came through the previous night, the payload was fully intact except for the placard I put on the outside of the payload with my contact information which would explain why I never got a call or text despite someone coming across it:

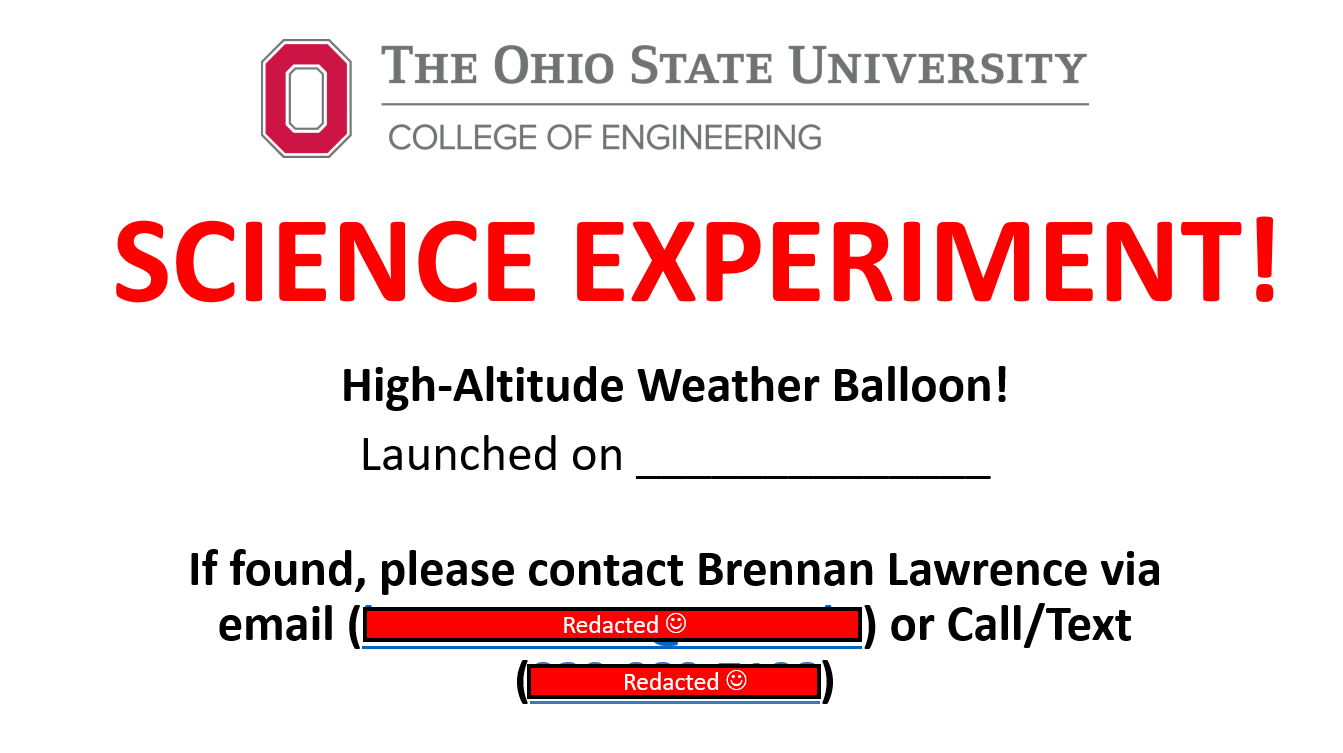
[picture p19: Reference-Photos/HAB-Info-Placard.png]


After thanking and saying goodbye to the landscaper that helped me find the payload, I first went to McDonalds to get something to eat (since I was too focused on finding the payload and didn't want to stop beforehand) and then went into a nearby parking lot in order to get the micro-SD cards out of the payload and check the data. Thankfully, everything seemed to be intact which was amazing! I gave it a once-over just to see what kind of results we got and then drove back to campus so I could look at all the data more closely.

Upon further inspection, I noticed several things. Firstly, the balloon remained on until 3am on 4/10/24 which, if we were searching closer to this area, leads me to believe that we would've been able to find it via the radio. Secondly, there appeared to be about an hour gap in the data due to the GPS not connecting at the extremely high altitude (about 70-80,000 feet). In hindsight, it was stupid to code the payload to only record data if it had a GPS signal since it lead to a gap of data but oh well. This was only something I could've figured out with more experience in these components. But regardless of this issue, we still got some interesting data! The coolest of which is the coordinates the payload logged:

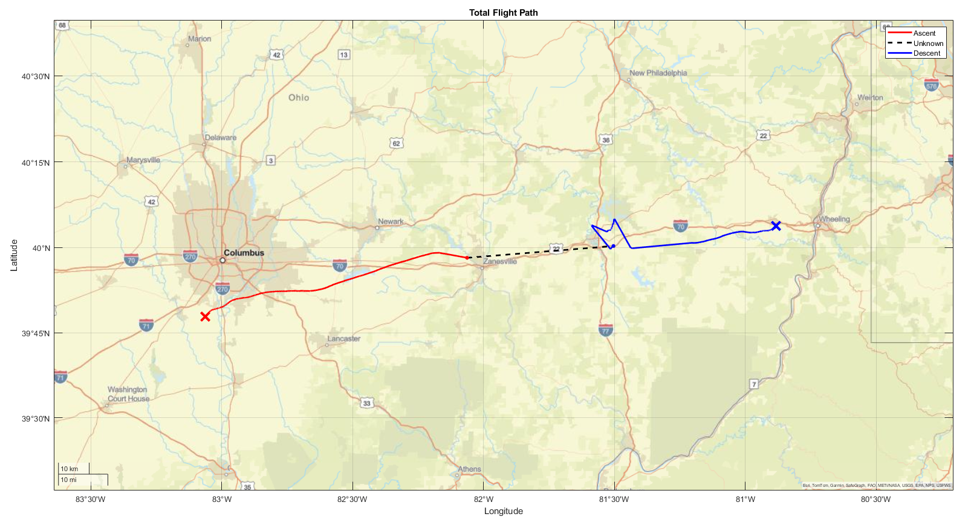
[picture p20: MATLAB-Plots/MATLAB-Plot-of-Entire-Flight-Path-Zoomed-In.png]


So overall, the website we used to estimate the flight path was pretty close to the one the balloon actually followed which is incredible. Likewise, the balloon appeared to have performed even better than intended since it drifted about 20 miles further east than we expected. This leads us to believe that the balloon reached an altitude closer to 110,000 ft instead of the anticipated 100,000 ft. And speaking of which, these following two plots of both the GPS altitude and the pressure corresponding to the recorded pressures were created:

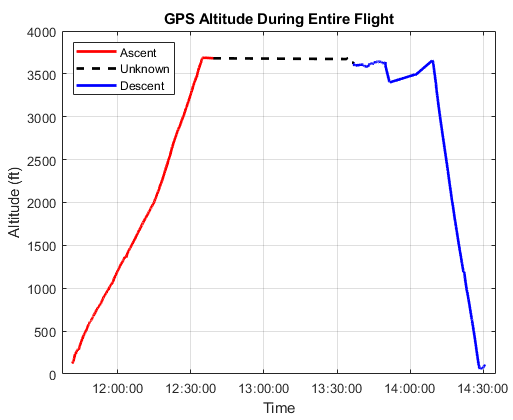
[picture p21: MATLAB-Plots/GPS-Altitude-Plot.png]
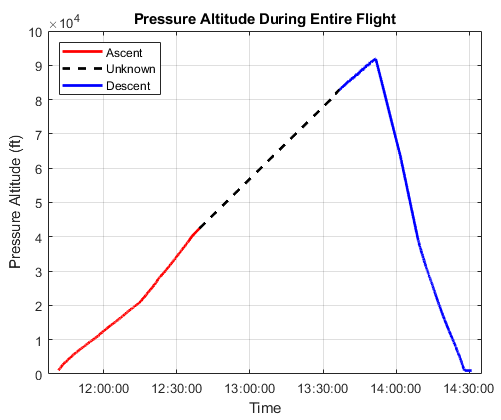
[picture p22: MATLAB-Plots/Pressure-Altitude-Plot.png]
 

The GPS altitude is definitely way, wayyyyy off from what was actually recorded. Honestly I don't know why since I would've assumed it would've been able to figure this out by the triangulation of the satellites it connected to but it apparently didn't. But thankfully, when looking at the recorded pressures and comparing that to standard atmosphere pressure tables, our altitude appears to be much more realistic and what we expected! The GPS altitude stated we only got to an altitude of 3,688.38 ft while the pressure tables returned a max altitude of 91,870.25 ft. We do believe the balloon went a bit higher than this altitude given the distance it drifted and the GPS cutting out at too high of an altitude.

Likewise, we also collected both the interior and exterior temperature for plotting:

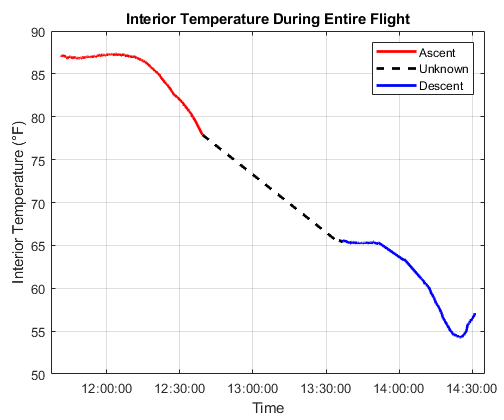
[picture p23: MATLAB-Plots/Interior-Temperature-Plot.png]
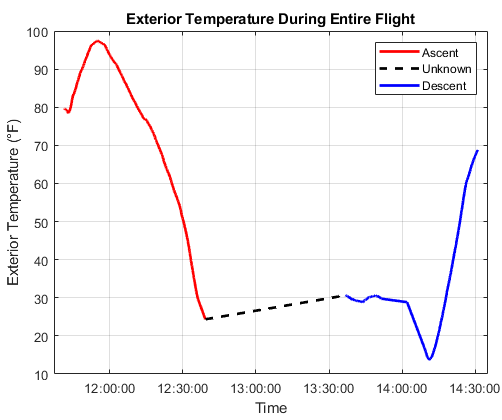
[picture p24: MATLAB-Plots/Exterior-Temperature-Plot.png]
 

The interior temperature returned values that we expected on account of the handwarmer keeping the internal temperature of the payload within acceptable temperatures throughout the entire flight. Likewise, the interior temperature slowly decreased throughout the flight which makes sense due to the ambient temperature outside getting colder and colder which would've seeped into the inside of the payload. Furthermore, the exterior temperature appeared to be kind of skewed due to the handwarmer used to keep the payload electronics warm. We had to tuck our exterior temperature sensor between the styrofoam shell and outer bubblewrap layer which I believe caused the exterior temperature sensor to become warmed up by the handwarmer slowly warming the styrofoam shell. Despite this, we still saw a steep decrease in ambient temperature (minimum of 13.66°F) which was much, much colder than the ground temperature when we launched!

And then finally, we also collected ambient pressure during the entire flight. We tried to do a small halo of tubing that connected to the pressure sensor in order to get a pressure reading at the top, side, and bottom of our payload in order to get an averaged pressure reading:



The pressure data, despite the gap in data, shown the exact same trend that we were expecting from our simulations. It had a nice sort of parabolic shape to it and ended up having a minimum pressure of 0.23 psi (1585.79 Pascals) which was similar to what we were expecting before we launched which was great!

Overall, we got a bunch of cool data from our launch and I am incredibly thankful that the Air Tag was able to save our project/payload from being completely lost. All the data collected lined up rather similarly to what we expected which was amazing for our hypothesis that we came up with at the beginning of the school year. I'm a bit dissapointed that the way our balloon payload was coded caused it to stop collecting data at high altitudes due to the GPS not getting a signal from any satellites, but I am happy that it worked for the most part! If I were to use this payload again as is, I would stick to a smaller balloon like a 100 or 200 gram balloon that would reach a slightly shorter altitude (about 30,000-40,000 ft) in order to prevent the GPS from disconnecting. And with proper changes to the code, I would run the payload again as is in order for it to collect data despite not having a GPS signal.

## Flight Test Data Comparison to Simulation Code

And just because I had to do it for our presentation and final report for the class this project was for, here are the plots that I created that compares the data collected from our Flight Test to the code I wrote that simulated our weather balloon launching. The code itself is located in the [MATLAB Comparison](MATLAB-Comparison-Plots-And-Code) folder! The first one is temperature:

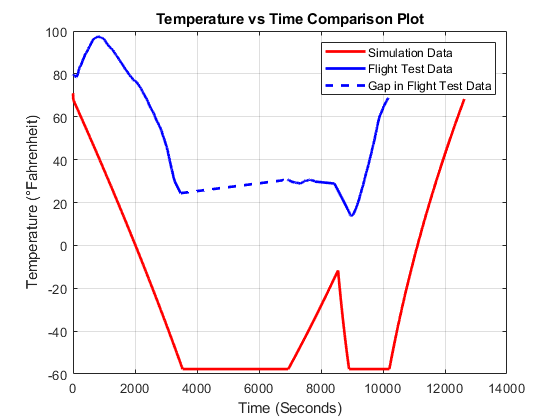
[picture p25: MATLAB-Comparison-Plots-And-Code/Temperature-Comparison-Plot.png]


As can be seen in this plot, the flight test data is definitely skewed due to the handwarmer warming up the styrofoam enough to cause the exterior temperature sensor to also become warm. The neat thing to note, however, is that the exterior temperature sensor appeared to follow the same trend as the simulation code, which is based off of the standard atmosphere model. The Flight Test temperature data shows an initial clear, steep decrease in temperature followed by it seemingly staying constant/slightly increasing. This was then followed by the temperature decreasing for a little while before it drastically increasing as the balloon fell closer and closer back to the Earth's surface.

Likewise, here is the plot for pressure:

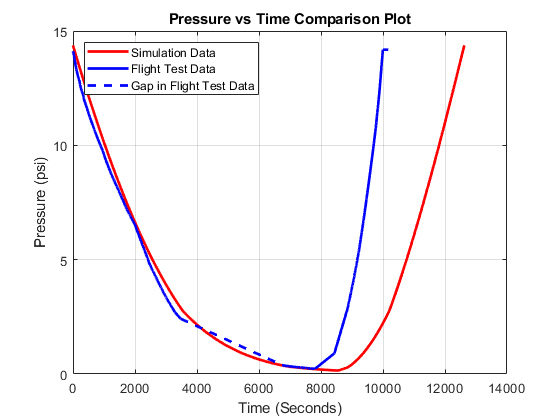
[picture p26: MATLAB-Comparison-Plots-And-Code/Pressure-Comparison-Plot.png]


The flight test data for pressure honestly couldn't have been more close to be completely honest. It showed the exact same trend to the simulated results with only the pressure increasing sooner in the Flight Test data. This could be due to the descent rate being much faster than what was calculated in the simulated data and shouldn't really be looked too deep into. The important thing is just how they showed the same trend and honestly ended up with very similar minimum pressures which is amazing!

And then finally, here is a plot for altitude. Please note that this plot was created using the pressure altitude calculated via the pressure collected during the Flight Test:

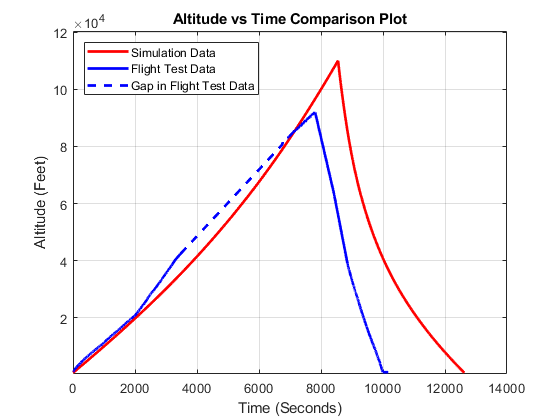
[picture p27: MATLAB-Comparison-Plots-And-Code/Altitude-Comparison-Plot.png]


Again, the flight test data for altitude was almost spot on like with pressure. The only differences are again, the altitude decreasing quicker than the simulation again (for similar reasons just stated previously) along with the flight test data appearing to show that the balloon reached a maximum altitude of about 20,000 ft. The biggest reason for this difference is that the code assumes that the balloon reaches the user-input target altitude, which in this case was 110,000 ft like the manufacturer specified. I'm sure with more tinkering that the simulation would match up closer to the data collected here, however I do think that the gap in data caused by the loss of GPS connection to also be to blame for the altitude collected from the flight test data. If it collected temperature and pressure for the entire flight, I think we could have closer curve to the flght test data!

## Photo Results

We got TONS of photos from our payload which I included all of them in the [Raw Payload Photos](Raw-Payload-Photos) folder. However, to save you time while also showing the coolest/funniest photos we got from the payload, I picked out a couple photos from the hundreds we got. Here are some of them along with a small description:

#### First photo following launch

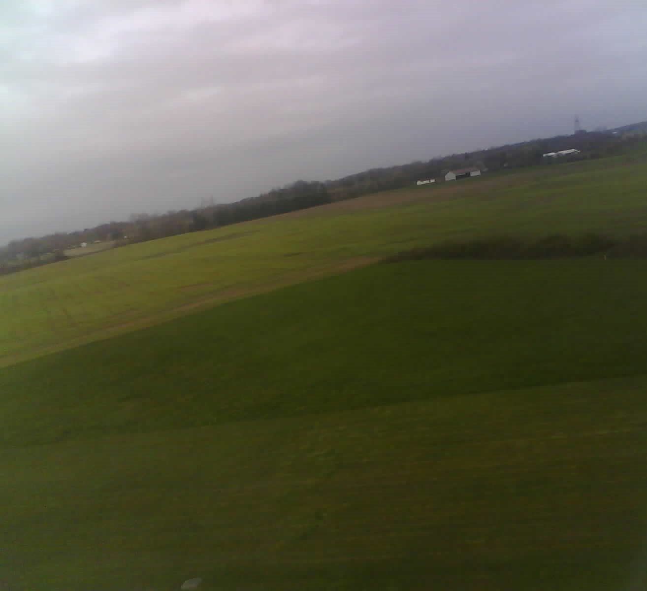
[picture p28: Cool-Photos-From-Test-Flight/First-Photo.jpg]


#### First photo above the clouds (Ascent)

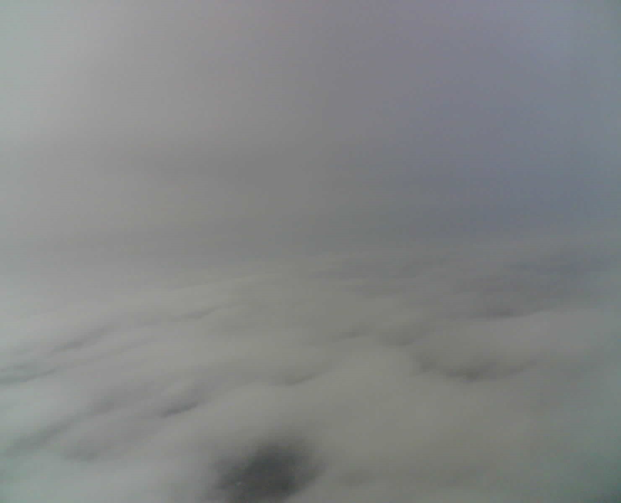
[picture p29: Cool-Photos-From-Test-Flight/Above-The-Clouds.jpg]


#### Cool photo of the clouds (Ascent)

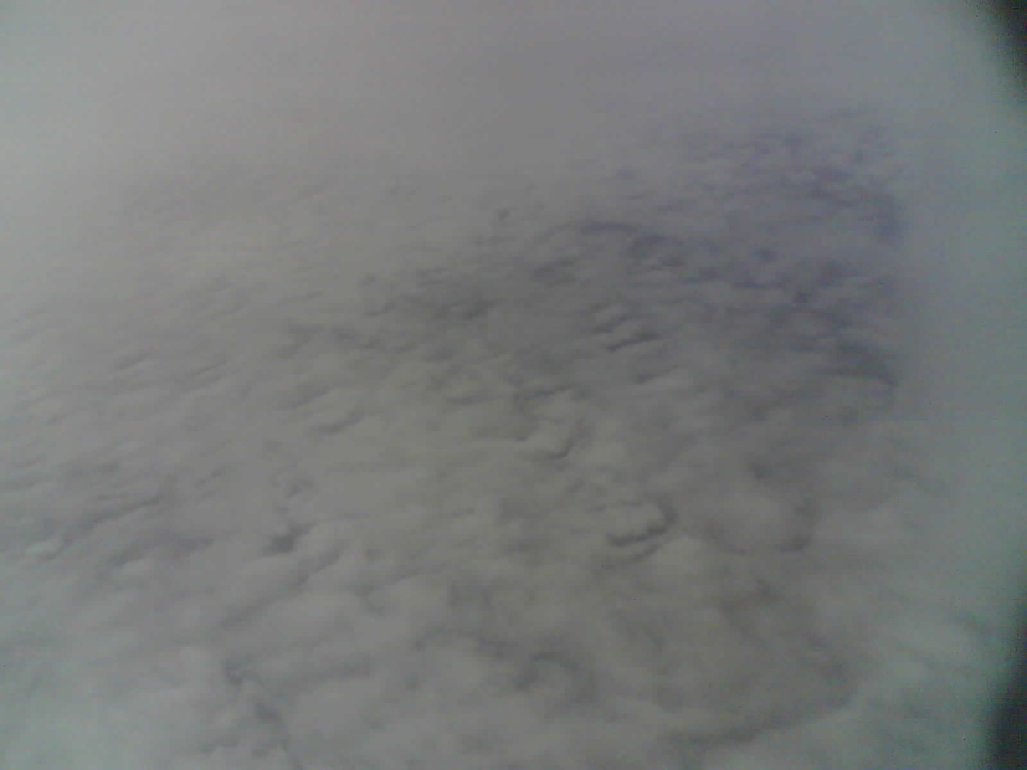
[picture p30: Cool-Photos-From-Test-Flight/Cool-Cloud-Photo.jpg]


#### Balloon swinging during descent photo

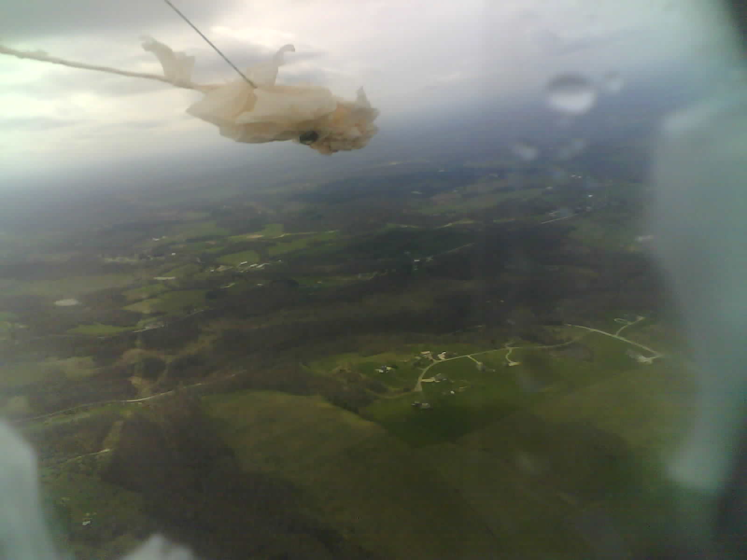
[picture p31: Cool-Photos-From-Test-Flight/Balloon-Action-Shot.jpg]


#### First photo after landing

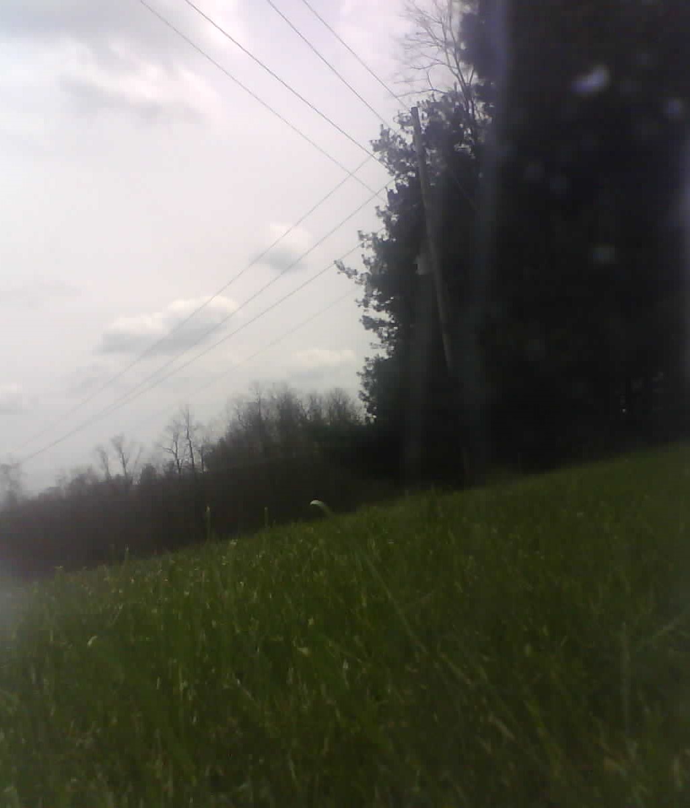
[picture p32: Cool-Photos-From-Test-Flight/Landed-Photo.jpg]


#### Earth curvature photo 1

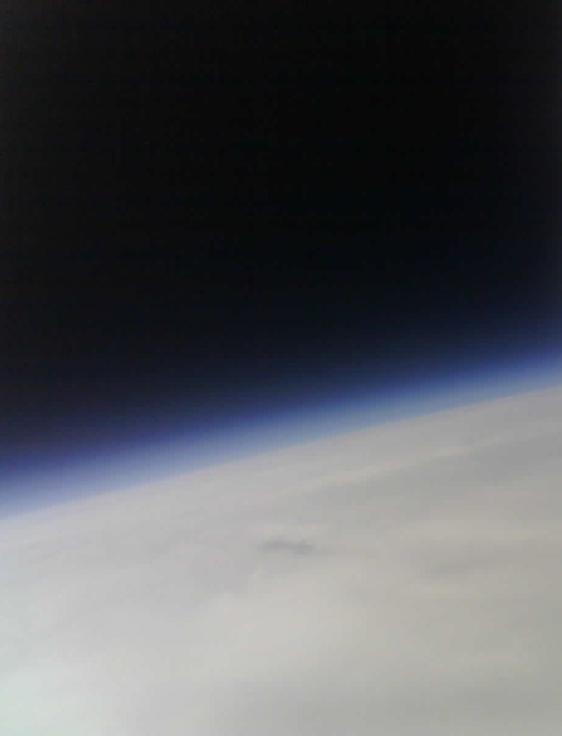
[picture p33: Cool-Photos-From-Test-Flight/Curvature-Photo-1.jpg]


#### Earth curvature photo 2



#### Earth curvature photo 3

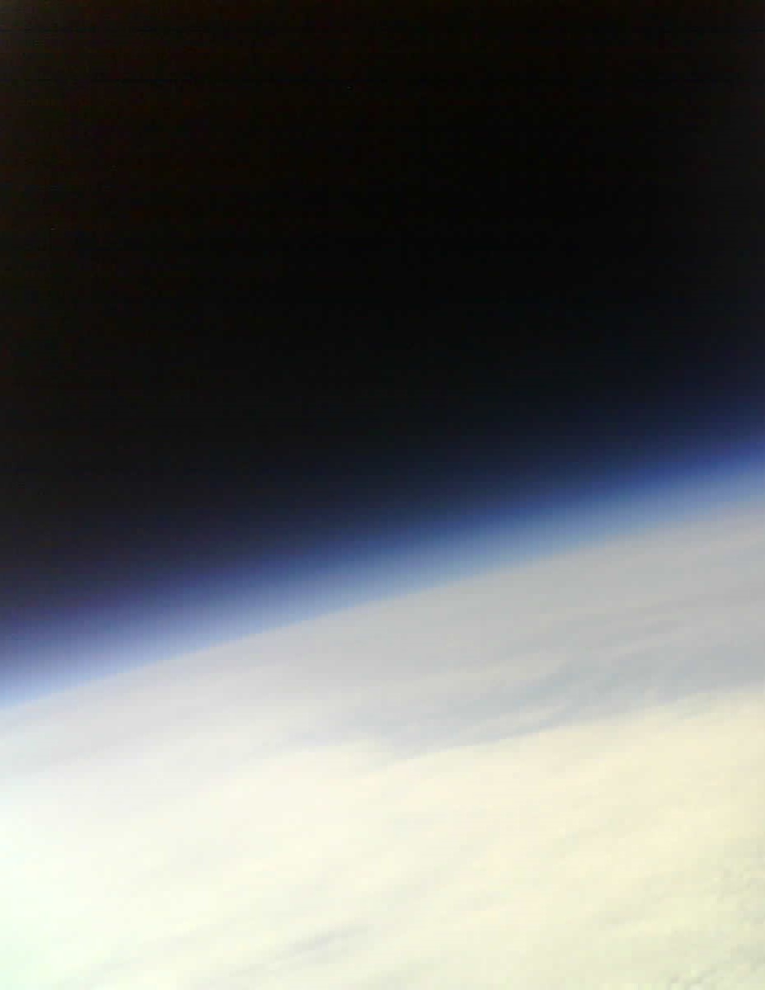
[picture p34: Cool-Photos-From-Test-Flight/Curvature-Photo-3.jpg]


#### Cool Descent photos

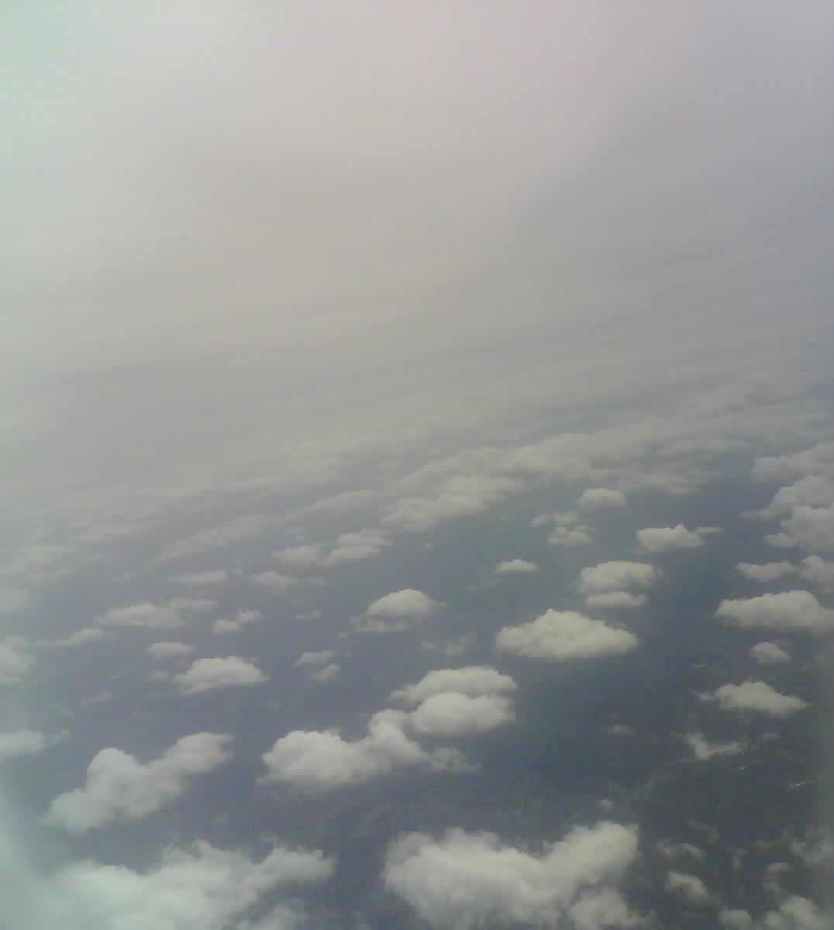
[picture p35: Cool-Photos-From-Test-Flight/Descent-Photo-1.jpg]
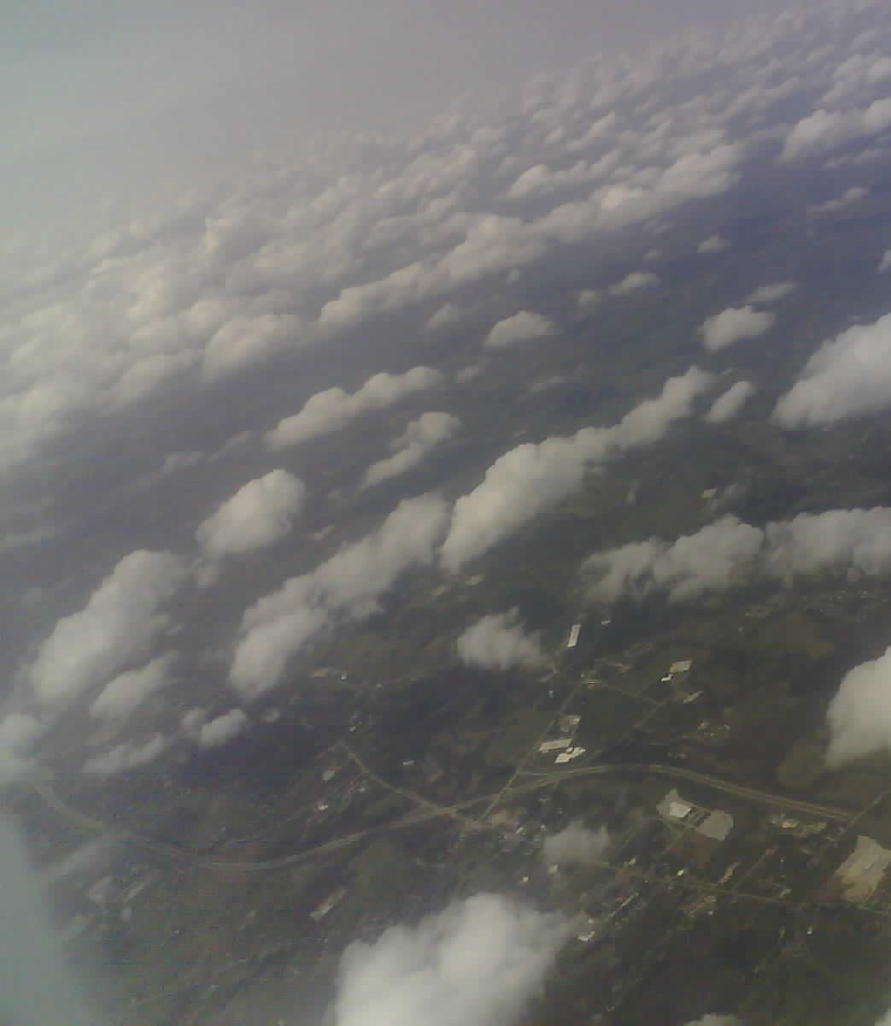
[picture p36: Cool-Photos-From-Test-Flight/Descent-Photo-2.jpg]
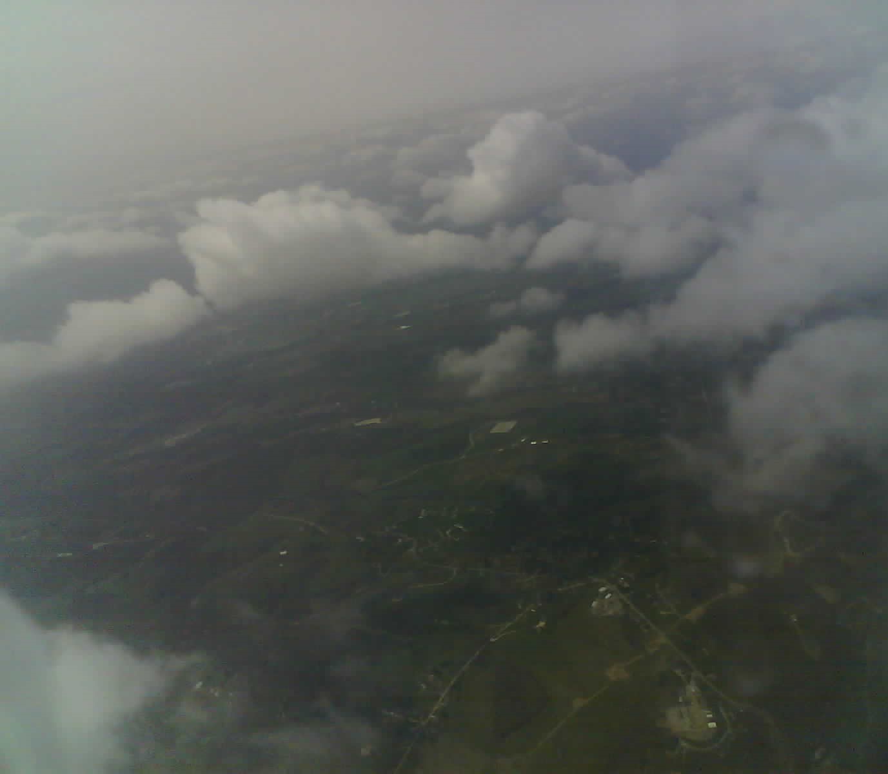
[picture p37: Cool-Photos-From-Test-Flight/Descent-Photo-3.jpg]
  

#### Visitor photos

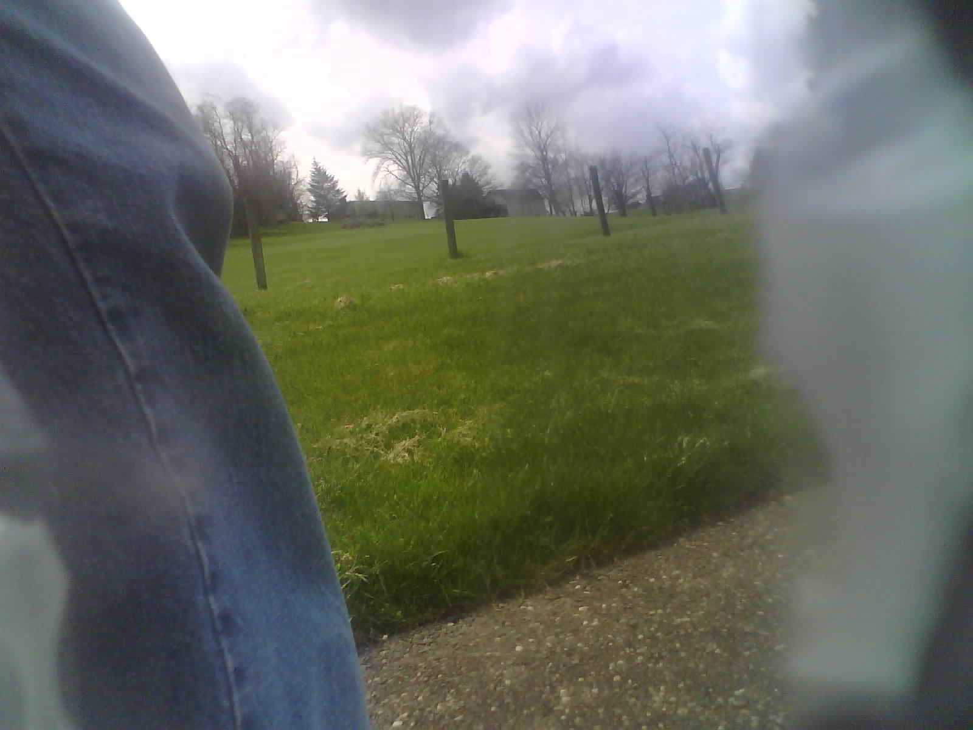
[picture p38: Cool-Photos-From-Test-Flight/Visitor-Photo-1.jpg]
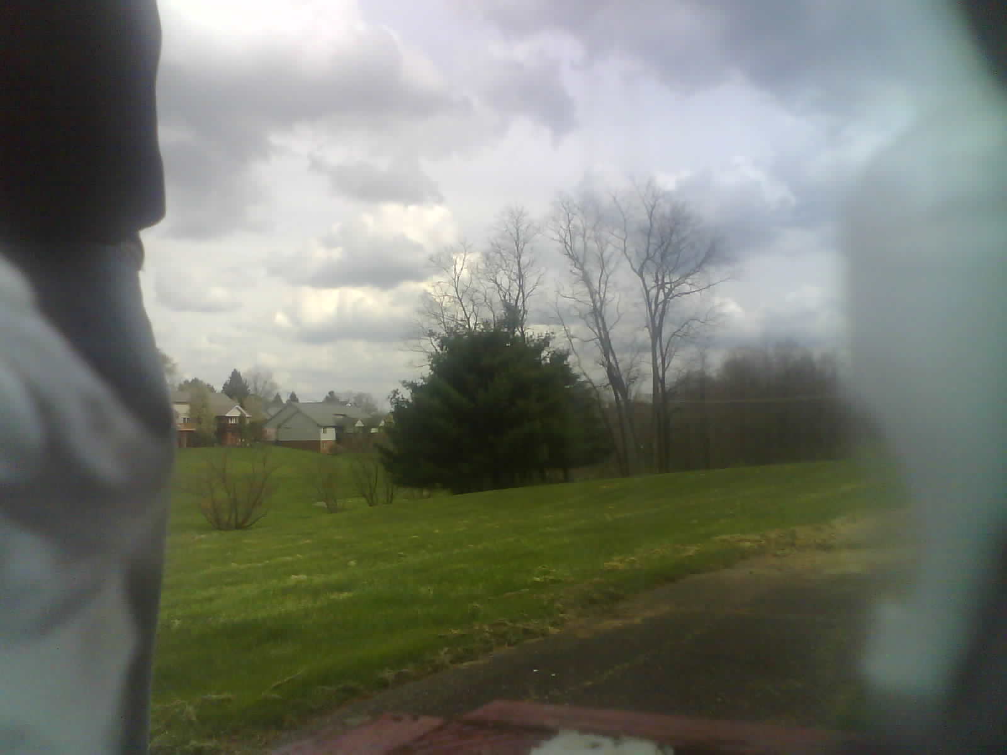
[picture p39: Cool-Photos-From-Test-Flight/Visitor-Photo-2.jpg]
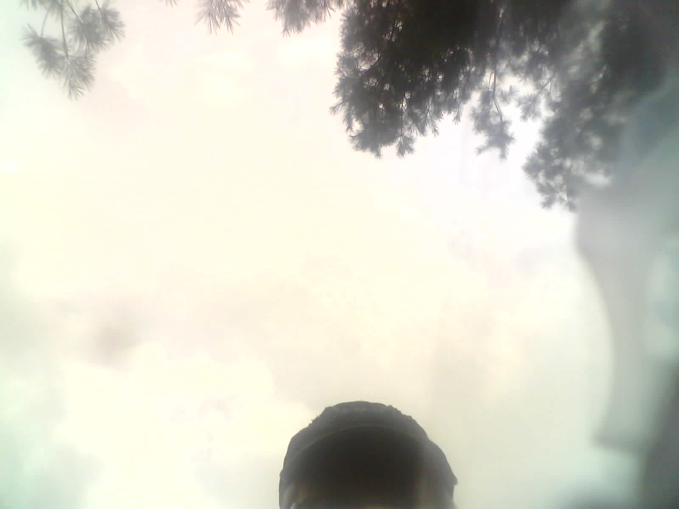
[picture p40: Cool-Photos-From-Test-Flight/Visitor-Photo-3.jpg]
  

## Suggestions for Improvements

From the start of this project, I was in close conversations with our faculty advisor who has much, much more experience with unmanned aircraft and the like. He originally showed us [APRS.fi](https://aprs.fi/#!lat=40.0&lng=-83), a nifty website that shows all the radio towers and devices that are using frequencies allowed to those who have an amateur radio license (144. 390 MHz). Due to myself or anyone in my group not in possession of this license, we were going to have to use our faculty advisor's with our original plan for our project. However, after some digging online, I discovered the Arduino MKR WAN 1310 board that had a radio module built right into the board itself. This struck me as really cool and decided to use this board without giving it much thought that it could only output on either 915 MHz, 868 MHz, or 433 MHz. So using this specific arduino board to handle transmitting our data packets, we were no longer going to be able to use the APRS.fi website which sucked since it seemed amazing for tracking devices such as a high-altitude balloon.



#### Example of an APRS.fi-compatable radio module (Sadly, I don't think its produced anymore)

That's where the tracking reciever came into fruition since my idea would be to have someone (me) go driving after it in a vehicle along its entire flight path instead of letting it go and waiting for it to start showing up on the APRS.fi website. I say all of this to lead up my suggestion: I reccommend trying to change the way data is being transmitted with our original design. I think axing the Arduino MKR WAN 1310 board idea and instead going with something like an Arduino nano or an Arduino MKR ZERO and either finding or building a dedicated radio module that can use amateur radio license frequencies would be a better idea. I found a couple online, but most seemed very above my skill level and out of our given budget of $600. However, there are plenty of ideas and attemps that I found online by just doing a simple [google search](https://www.google.com/search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) that seemed really promising. Overall, I would like to keep tinkering with this once I graduate in my free time since I really enjoyed this project and would like to keep messing with this stuff well into the future. I intend on getting my amateur radio operator license once I have some more free time in order to try and expand this project into a very robust product.

A second suggestion that I would like to see with this project is honestly replacing the need for a proprietary Arduino board and instead design and print a new micro-controller board that can take its place. My thought process for this is that it would help do the following things:
  - Cut weight by being more compact
  - Cheaper in the long run
  - Marketable to individuals or companies that deal with HAB's

So I think by making an all-in-one micro-controller meant for this project specifically, we could end up with a simple board that would just need temperature sensors, a pressure sensor, and a radio module to be plugged into it for it to operate as intendended. My idea would be that a micro-controller specifically designed for this project would already have both a GPS and RTC board on it already since these would need to be present regardless while still giving the end-user the ability to choose their own preferred sensors and radio module. Another idea would maybe making two versions of this board: a 'lite' one if you will that wouldn't support a camera and be slightly cheaper than the second 'more expensive' board that would be capabale of supporting a camera similar to the Arducam OV2640 camera I mentiond prior in this page. The bigest different between these two boards would be its included RAM since I still believe that is why I couldn't get the Arducam OV2640 to work originally and needed to switch to the ESP32-CAM board.

Doing some research for this idea lead me to [OpenTrack](https://protofusion.org/wiki/opentrack), which appeared to do pretty much everything that I have talked about. It addresses my idea of changing the radio and still has a bunch of moduality for temperature sensors, pressure sensors, and more to be added. Overall, this is something that I wish I would have looked more into at the beginning of this project.

I'm sure there are plenty of other suggestions to change with this project, however these are the two that I immediately thought of when trying to do some reflecting at the end of the project. If you have any ideas or suggestions, or even already changed things on your end, I would love to hear about it! I am a big novice when it comes to this sort of stuff so I know plenty of people could improve immensely on the work laid out here.

## Final Thoughts and Reflection

Overall, I had a crazy amount of fun and enjoyment while tackling this project. I have always had an interest in 3D printing, tinkering with electronics, and CAD just to name a few of the applicable ones to this project, so I was happy to finally find that same enjoyment in my coursework. This project taught me a lot about researching and formulating design ideas in order to refine and bounce off of others throughout the course of the semester. Likewise, I was able to gain some vital skills in project and time management, groupwork, presentation and public speaking, and document coordination. Honestly, I know it may not look super fancy, but I am so proud from turning this:



Into this:



Just going from my little breadboard prototyping station to a fully assembled chassis was so rewarding and honestly made me absolutely giddy with excitement. And not to mention it worked first try after I finished putting it all together which was even better.

Likewise, I have never launched a balloon before and had to learn all the steps to do so. It was honestly easier than I expected which was a nice surprise. It all boiled down to making sure all the rigging was correct and connected properly, along with making sure I didn't touch the damn balloon with my greasy hands. I always expected launching these balloons to be insanely difficult, but it really just involved paracord, zip ties, and electrical tape. Plus it was so relieving watching our HAB launch and drift away; almost like all of my troubles and frustrations went away with it since I knew with the launch was coming my graduation that has taken every bit of effort out of me.

I have a lot of things that, if I had more time and money, I would have loved to spend more time on and improve (mainly the things I outlined above in suggestions). I poured my heart and soul into this project; not to mention my own money since I stretched the budget given to us from the course as thin as possible and needed a bit more (for things such as helium, antennas, PLA filament, wire, solder, and more). My hope is that this project is offered again in the future for new engineering students to try their hand at it. I would hope they look at this project as a baseline and improve upon it in anyway that they seem fit. My major suggestions for that is don't buy 4 balloons, you will be lucky to get 2, if not only 1 launch. And seriously, try and get everything done as soon as you and your group can. Don't wait until the day of to do the papers, reports, and presentations because it really gets tiring after a while; not to mention you will not want to see this project by the end of your senior year.

## Useful Online Tools

The first useful online tool that I used for this project was this [Balloon Perfomance Calculator](https://www.highaltitudescience.com/pages/balloon-performance-calculator) created by High Altitude Science. I liked using this for seeing how much helium I needed for my balloon-payload setup and ensuring that it would reach my target altitude.

The second useful online tool I used for this project was this [Flight Path Predictor](https://predict.sondehub.org/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) created by Jon Sowman, Adam Grieg, and Daniel Richman of Cambridge University. I found this tool later into this project and honestly it was really cool to use and predict where we would expect our balloon to drift to depending on the day/time/weather/altitude. [PUT IN BLURB ABOUT HOW THIS WAS COMPARED TO OUR ACTUAL FLIGHT TEST].

## Resources and Inspirations

The biggest inspiration that I found that helped immensely with conducting this project and designing this github for other interested individuals and future engineering students was a fellow individual by the name of [blazerunner44](https://github.com/blazerunner44/Arduino-High-Altitude-Balloon?tab=readme-ov-file#user-content-balloon-payload). I loved the work he did and I tried my best to emulate his project despite my more limited skillset.

Likewise, the hundreds of other online blogs, papers, and individuals I approached for help on this project gave so many great ideas that we encorporated into our own project. We gained a great understanding of what we needed to consider in our design as well as came up with ideas to incorporate into our own project that we initially didn't think of.

## Acknowledgements

- A big thank you to our faculty advisor for this project. I figure I won't put his name on here out of respect for his privacy, but he knows who he is and he was an incredible resource to turn to. I hope he conducts this project or something similar in the future, I think future students in the department would really enjoy what he would offer!
- Thank you to our course advisor for this project. Again, I won't put his name on here also out of respect for his privacy, but he was very helpful for keeping us on track and teaching us vital skills required to join the workforce in the near future
- Thank you to our GTA, he was super nice and helpful when we approached him with questions
- Thank you to BALLOONIACS, if it wasn't for their company we wouldn't have been able to get helium in time and get our project off the ground (literally)!
- Thank you to my parents, grandparents, sister, and girlfriend. You all were a major source of support throughout my education as you very well know and I greatly appreciate it. I wouldn't have been able to make it to where I am today without you all.
- Monster Energy Drinks and Redbull. Caffeine is the only thing that got me through all my coursework. I spent plenty of all nighters getting this project to where it ended up and it was because of these bad boys I was able to do so.

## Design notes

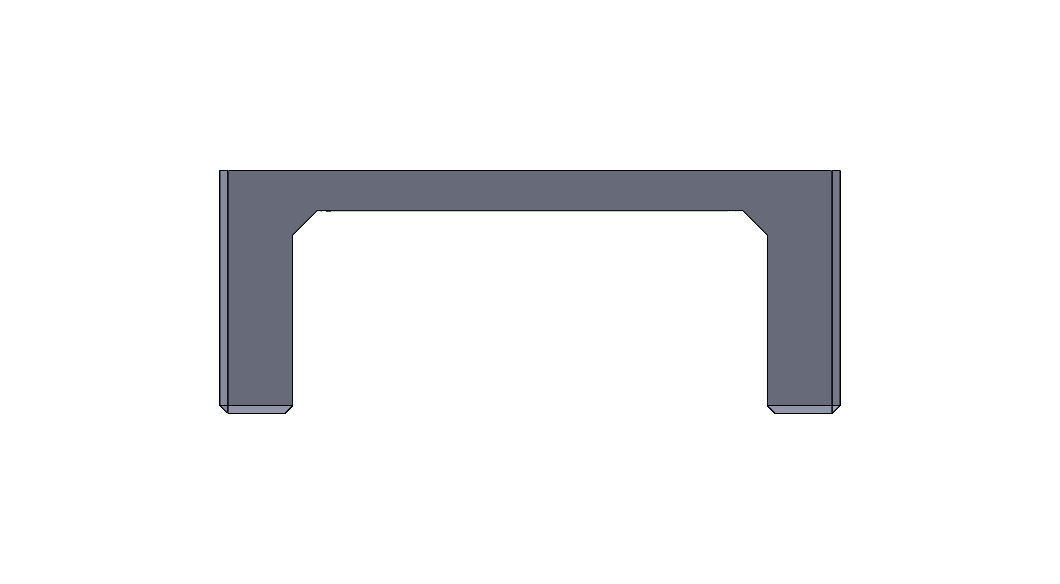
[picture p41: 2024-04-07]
Payload-Chassis-CAD-Folder/Payload-Chassis-Arduino-Bracket-Photos/Payload Chassis Arduino Bracket Left-View Photo.PNG

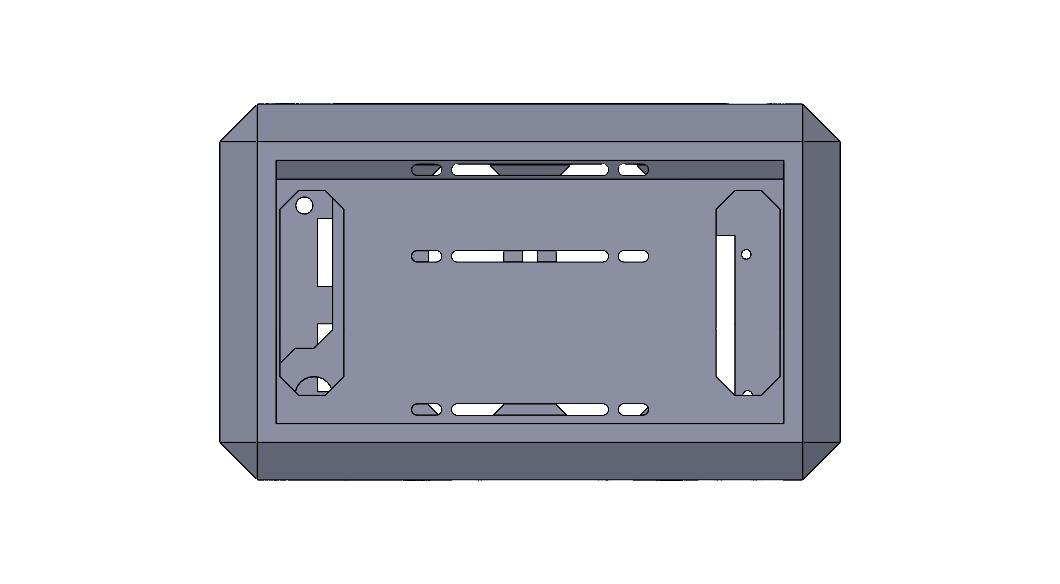
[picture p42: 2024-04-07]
Payload-Chassis-CAD-Folder/Payload-Chassis-Shell-Photos/Payload Chassis Shell Left-View Photo.PNG

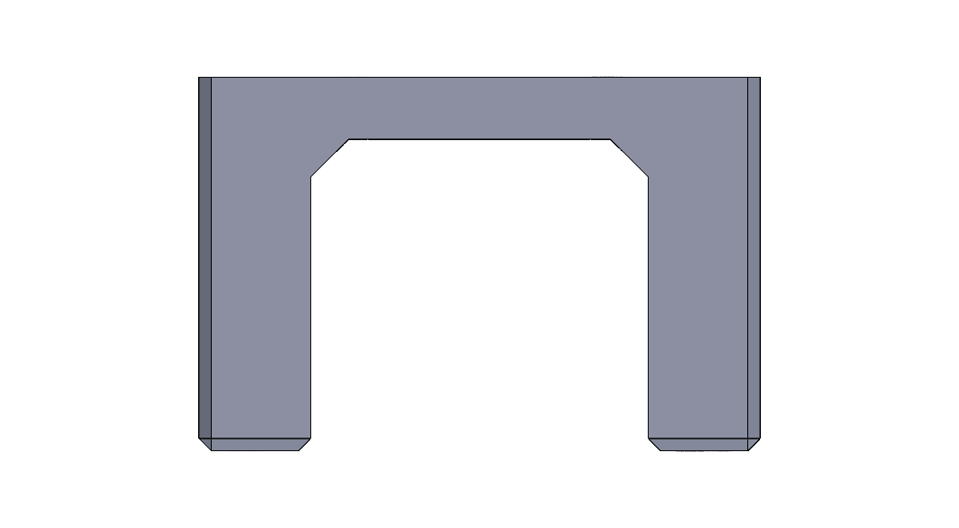
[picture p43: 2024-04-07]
Payload-Chassis-CAD-Folder/Payload-Chassis-Arduino-Bracket-Photos/Payload Chassis Arduino Bracket Back-View Photo.PNG

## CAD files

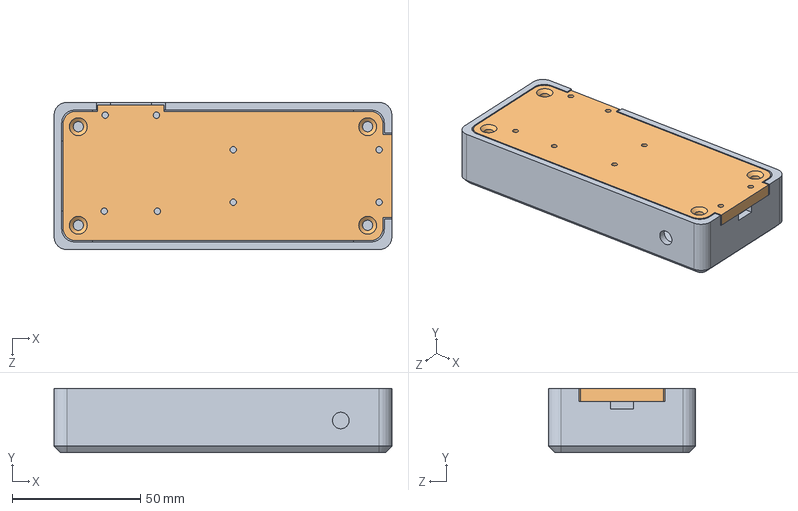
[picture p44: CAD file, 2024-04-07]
Tracking-Reciever-CAD-Folder/Tracking-Reciever-Solidworks-Files/Reciever Assembly.SLDASM
132.0 x 25.0 x 57.5 mm
Top
Bottom

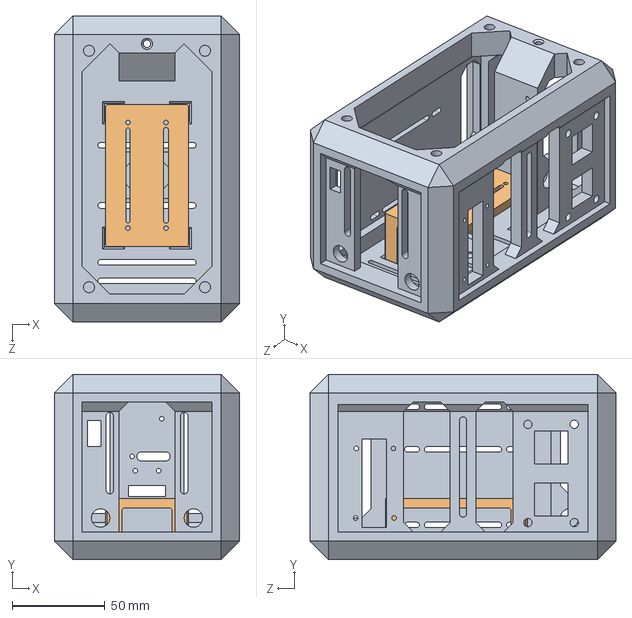
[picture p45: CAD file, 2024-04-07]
Payload-Chassis-CAD-Folder/Payload-Chassis-Solidworks-Files/HAB Chassis Rev. 2 Assembly.SLDASM
100.0 x 100.0 x 165.0 mm
HAB Chassis Rev. 2
Hab Chassis Rev. 2 Arduino Bracket

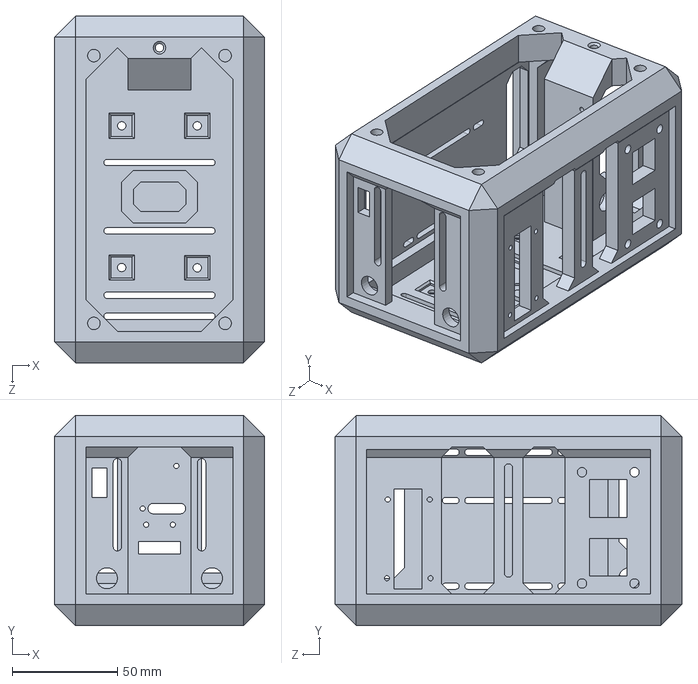
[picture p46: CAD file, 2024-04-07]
Payload-Chassis-CAD-Folder/Payload-Chassis-Solidworks-Files/HAB Chassis Rev. 2.SLDPRT
100.0 x 100.0 x 165.0 mm

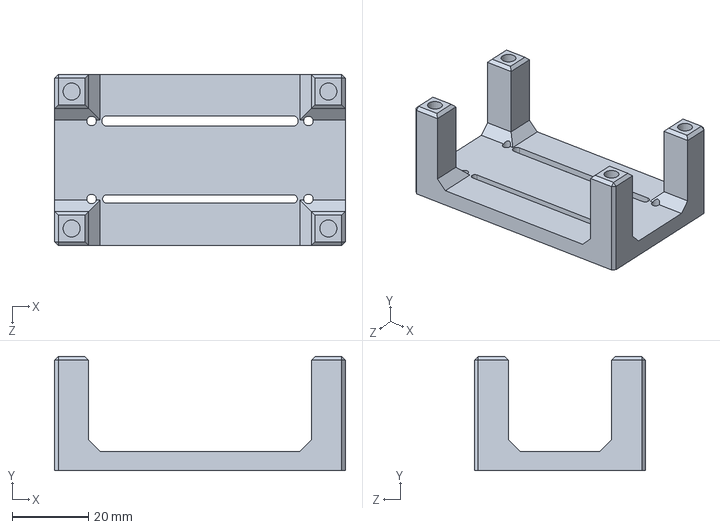
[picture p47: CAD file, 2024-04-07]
Payload-Chassis-CAD-Folder/Payload-Chassis-Solidworks-Files/Hab Chassis Rev. 2 Arduino Bracket.SLDPRT
76.5 x 30.0 x 45.0 mm

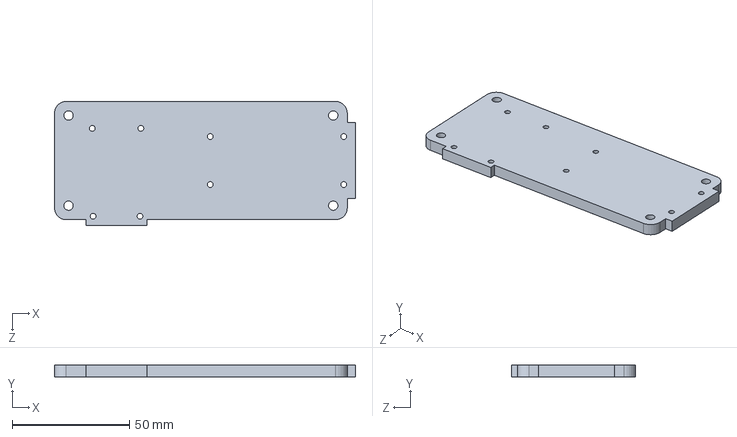
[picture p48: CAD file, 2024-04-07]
Tracking-Reciever-CAD-Folder/Tracking-Reciever-Solidworks-Files/Bottom.SLDPRT
128.5 x 5.00 x 53.0 mm

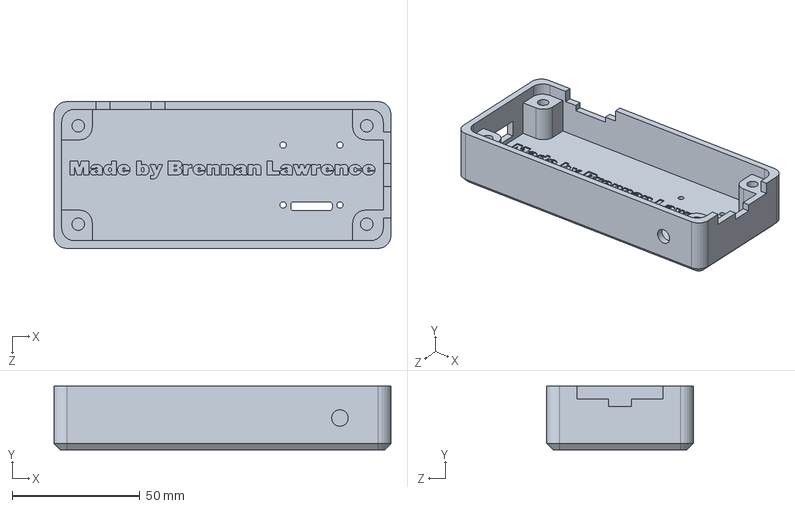
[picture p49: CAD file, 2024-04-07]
Tracking-Reciever-CAD-Folder/Tracking-Reciever-Solidworks-Files/Top.SLDPRT
132.0 x 25.0 x 57.5 mm

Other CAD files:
Payload-Chassis-CAD-Folder/Payload-Chassis-Printing-Files/HAB Chassis Rev. 2.STL
Payload-Chassis-CAD-Folder/Payload-Chassis-Printing-Files/Hab Chassis Rev. 2 Arduino Bracket.STL
Tracking-Reciever-CAD-Folder/Tracking-Reciever-Printing-Files/Bottom.STL
Tracking-Reciever-CAD-Folder/Tracking-Reciever-Printing-Files/Top.STL

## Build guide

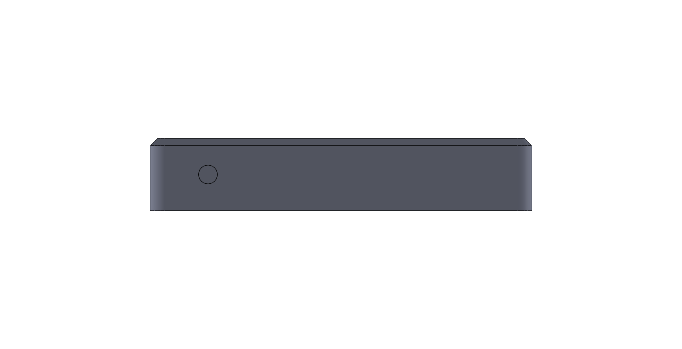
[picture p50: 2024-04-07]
Tracking-Reciever-CAD-Folder/Tracking-Reciever-Assembly-Photos/Tracking-Reciever-Assembly-Left-View-Photo.PNG

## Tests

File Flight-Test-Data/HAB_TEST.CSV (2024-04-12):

Date(YYYY-MM-DD) | Timestamp(HH:MM:SS) | Interior_Temperature_(°F) | Exterior_Temperature_(°F) | Pressure_(psi) | Latitude(°) | Longitude(°) | Altitude(ft) | #_of_Satellites
2024/4/2 | 11:8:59 | 68.90 | 74.41 | 14.36 | 39.7955780 | -83.0645676 | 74.22 | 4.00
2024/4/2 | 11:9:1 | 69.01 | 74.52 | 14.36 | 39.7955780 | -83.0645676 | 74.19 | 4.00
2024/4/2 | 11:9:3 | 69.01 | 74.75 | 14.36 | 39.7955742 | -83.0645676 | 74.25 | 4.00
2024/4/2 | 11:9:5 | 69.01 | 74.75 | 14.36 | 39.7955742 | -83.0645676 | 74.25 | 4.00
2024/4/2 | 11:9:7 | 69.12 | 74.97 | 14.36 | 39.7955742 | -83.0645676 | 74.07 | 4.00
2024/4/2 | 11:9:9 | 69.12 | 74.97 | 14.36 | 39.7955780 | -83.0645676 | 74.13 | 4.00
2024/4/2 | 11:9:11 | 69.24 | 75.09 | 14.36 | 39.7955780 | -83.0645676 | 74.46 | 6.00
2024/4/2 | 11:9:13 | 69.24 | 75.20 | 14.36 | 39.7955742 | -83.0645676 | 74.40 | 6.00
2024/4/2 | 11:9:15 | 69.24 | 75.31 | 14.36 | 39.7955742 | -83.0645676 | 74.31 | 6.00
2024/4/2 | 11:9:17 | 69.24 | 75.43 | 14.36 | 39.7955742 | -83.0645676 | 74.34 | 7.00
2024/4/2 | 11:9:19 | 69.24 | 75.31 | 14.36 | 39.7955742 | -83.0645676 | 74.22 | 7.00
2024/4/2 | 11:9:21 | 69.35 | 75.31 | 14.36 | 39.7955742 | -83.0645676 | 74.22 | 7.00
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

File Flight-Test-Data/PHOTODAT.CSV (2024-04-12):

Date(YYYY-MM-DD) | Timestamp(HH:MM:SS) | Photo_Number | GPS_Altitude(ft)
2024/4/2 | 11:8:59 | 0 | 74.22
2024/4/2 | 11:9:15 | 1 | 74.31
2024/4/2 | 11:9:31 | 2 | 74.10
2024/4/2 | 11:9:47 | 3 | 73.88
2024/4/2 | 11:10:3 | 4 | 73.79
2024/4/2 | 11:10:19 | 5 | 74.04
2024/4/2 | 11:10:35 | 6 | 74.22
2024/4/2 | 11:10:51 | 7 | 74.34
2024/4/2 | 11:11:7 | 8 | 74.40
2024/4/2 | 11:11:23 | 9 | 74.80
2024/4/2 | 11:11:39 | 10 | 74.74
2024/4/2 | 11:11:55 | 11 | 74.55
2024/4/2 | 11:12:11 | 12 | 74.40
2024/4/2 | 11:12:27 | 13 | 74.58
2024/4/2 | 11:12:43 | 14 | 75.26
2024/4/2 | 11:12:59 | 15 | 74.98
2024/4/2 | 11:13:15 | 16 | 74.16
2024/4/2 | 11:13:31 | 17 | 74.19
2024/4/2 | 11:13:47 | 18 | 73.82
2024/4/2 | 11:14:3 | 19 | 73.73
2024/4/2 | 11:14:24 | 20 | 73.30
2024/4/2 | 11:14:41 | 21 | 73.33
2024/4/2 | 11:14:57 | 22 | 73.12
2024/4/2 | 11:15:13 | 23 | 72.66
2024/4/2 | 11:15:29 | 24 | 72.18
2024/4/2 | 11:15:45 | 25 | 71.99
2024/4/2 | 11:16:1 | 26 | 73.21
2024/4/2 | 11:16:17 | 27 | 72.60
2024/4/2 | 11:16:33 | 28 | 71.26
2024/4/2 | 11:16:49 | 29 | 70.81
2024/4/2 | 11:17:5 | 30 | 70.87
2024/4/2 | 11:17:21 | 31 | 71.08
2024/4/2 | 11:17:37 | 32 | 71.48
2024/4/2 | 11:17:53 | 33 | 72.18
2024/4/2 | 11:18:9 | 34 | 72.12
2024/4/2 | 11:18:28 | 35 | 71.48
2024/4/2 | 11:19:14 | 36 | 73.00
2024/4/2 | 11:19:35 | 37 | 72.97
2024/4/2 | 11:19:51 | 38 | 73.06
2024/4/2 | 11:20:18 | 39 | 75.22
2024/4/2 | 11:20:34 | 40 | 77.48
2024/4/2 | 11:20:50 | 41 | 74.62
2024/4/2 | 11:21:6 | 42 | 74.95
2024/4/2 | 11:21:22 | 43 | 71.66
2024/4/2 | 11:21:38 | 44 | 80.92
2024/4/2 | 11:21:54 | 45 | 83.58
2024/4/2 | 11:22:10 | 46 | 83.61
2024/4/2 | 11:22:26 | 47 | 79.98
2024/4/2 | 11:22:42 | 48 | 76.99
2024/4/2 | 11:22:58 | 49 | 74.16
2024/4/2 | 11:23:14 | 50 | 76.99
2024/4/2 | 11:23:30 | 51 | 76.54
2024/4/2 | 11:23:46 | 52 | 75.19
2024/4/2 | 11:24:2 | 53 | 73.33
2024/4/2 | 11:24:18 | 54 | 72.82
2024/4/2 | 11:24:34 | 55 | 72.57
2024/4/2 | 11:24:50 | 56 | 72.66
2024/4/2 | 11:25:7 | 57 | 72.85
2024/4/2 | 11:25:23 | 58 | 79.92
2024/4/2 | 11:25:39 | 59 | 76.63
2024/4/2 | 11:25:55 | 60 | 76.23
2024/4/2 | 11:26:11 | 61 | 76.81
2024/4/2 | 11:26:28 | 62 | 76.02
2024/4/2 | 11:26:44 | 63 | 75.07
2024/4/2 | 11:27:0 | 64 | 74.49
2024/4/2 | 11:27:16 | 65 | 73.24
2024/4/2 | 11:27:32 | 66 | 72.18
2024/4/2 | 11:27:48 | 67 | 72.85
2024/4/2 | 11:28:4 | 68 | 72.51
2024/4/2 | 11:28:20 | 69 | 72.33
2024/4/2 | 11:28:36 | 70 | 72.57
2024/4/2 | 11:28:52 | 71 | 72.82
2024/4/2 | 11:29:8 | 72 | 72.51
2024/4/2 | 11:29:24 | 73 | 73.18
2024/4/2 | 11:29:40 | 74 | 76.26
2024/4/2 | 11:29:56 | 75 | 76.90
2024/4/2 | 11:30:12 | 76 | 77.48
2024/4/2 | 11:30:28 | 77 | 78.03
2024/4/2 | 11:30:44 | 78 | 76.87
2024/4/2 | 11:31:0 | 79 | 75.77
2024/4/2 | 11:31:16 | 80 | 74.95
2024/4/2 | 11:31:32 | 81 | 74.37
2024/4/2 | 11:31:48 | 82 | 74.40
2024/4/2 | 11:32:4 | 83 | 75.35
2024/4/2 | 11:32:20 | 84 | 77.97
2024/4/2 | 11:32:36 | 85 | 75.10
2024/4/2 | 11:32:52 | 86 | 74.28
2024/4/2 | 11:33:8 | 87 | 73.33
2024/4/2 | 11:33:24 | 88 | 73.73
2024/4/2 | 11:33:40 | 89 | 74.71
2024/4/2 | 11:33:56 | 90 | 73.91
2024/4/2 | 11:34:12 | 91 | 74.55
2024/4/2 | 11:34:28 | 92 | 73.91
2024/4/2 | 11:34:44 | 93 | 73.94
2024/4/2 | 11:35:0 | 94 | 74.34
2024/4/2 | 11:35:16 | 95 | 75.83
2024/4/2 | 11:35:32 | 96 | 73.91
2024/4/2 | 11:35:48 | 97 | 73.06
2024/4/2 | 11:36:5 | 98 | 72.60
2024/4/2 | 11:36:21 | 99 | 72.94
2024/4/2 | 11:36:37 | 100 | 73.33
2024/4/2 | 11:36:53 | 101 | 74.04
2024/4/2 | 11:37:9 | 102 | 73.43
2024/4/2 | 11:37:34 | 103 | 73.09
2024/4/2 | 11:37:50 | 104 | 73.64
2024/4/2 | 11:38:6 | 105 | 73.33
2024/4/2 | 11:38:22 | 106 | 72.42
2024/4/2 | 11:38:38 | 107 | 71.60
2024/4/2 | 11:38:54 | 108 | 71.51
2024/4/2 | 11:39:10 | 109 | 71.96
2024/4/2 | 11:39:26 | 110 | 72.97
2024/4/2 | 11:39:42 | 111 | 73.49
2024/4/2 | 11:39:58 | 112 | 74.22
2024/4/2 | 11:40:14 | 113 | 74.83
2024/4/2 | 11:40:30 | 114 | 75.07
2024/4/2 | 11:40:46 | 115 | 75.26
2024/4/2 | 11:41:2 | 116 | 76.35
2024/4/2 | 11:41:18 | 117 | 104.97
2024/4/2 | 11:41:34 | 118 | 130.55
2024/4/2 | 11:41:50 | 119 | 151.73
2024/4/2 | 11:42:6 | 120 | 175.05
2024/4/2 | 11:42:23 | 121 | 209.31
2024/4/2 | 11:43:10 | 122 | 256.25
2024/4/2 | 11:43:35 | 123 | 282.46
2024/4/2 | 11:44:7 | 124 | 282.76
2024/4/2 | 11:44:23 | 125 | 320.74
2024/4/2 | 11:44:39 | 126 | 342.50
2024/4/2 | 11:44:55 | 127 | 363.57
2024/4/2 | 11:45:11 | 128 | 383.10
2024/4/2 | 11:45:28 | 129 | 403.59
2024/4/2 | 11:45:44 | 130 | 425.65
2024/4/2 | 11:46:0 | 131 | 444.79
2024/4/2 | 11:46:16 | 132 | 460.10
2024/4/2 | 11:46:32 | 133 | 475.03
2024/4/2 | 11:46:48 | 134 | 490.48
2024/4/2 | 11:47:4 | 135 | 505.27
2024/4/2 | 11:47:20 | 136 | 524.65
2024/4/2 | 11:47:36 | 137 | 545.74
2024/4/2 | 11:47:52 | 138 | 564.25
2024/4/2 | 11:48:8 | 139 | 580.64
2024/4/2 | 11:48:24 | 140 | 593.26
2024/4/2 | 11:48:40 | 141 | 605.61
2024/4/2 | 11:48:56 | 142 | 617.86
2024/4/2 | 11:49:12 | 143 | 630.33
2024/4/2 | 11:49:28 | 144 | 643.74
2024/4/2 | 11:49:44 | 145 | 658.22
2024/4/2 | 11:50:0 | 146 | 669.86
2024/4/2 | 11:50:16 | 147 | 686.50
2024/4/2 | 11:50:32 | 148 | 701.53
2024/4/2 | 11:50:48 | 149 | 716.43
2024/4/2 | 11:51:4 | 150 | 730.06
2024/4/2 | 11:51:20 | 151 | 744.23
2024/4/2 | 11:51:36 | 152 | 757.82
2024/4/2 | 11:51:52 | 153 | 769.96
2024/4/2 | 11:52:8 | 154 | 778.15
2024/4/2 | 11:52:24 | 155 | 789.10
2024/4/2 | 11:52:41 | 156 | 798.55
2024/4/2 | 11:52:59 | 157 | 815.10
2024/4/2 | 11:53:18 | 158 | 835.03
2024/4/2 | 11:53:34 | 159 | 852.07
2024/4/2 | 11:53:50 | 160 | 870.94
2024/4/2 | 11:54:6 | 161 | 887.30
2024/4/2 | 11:54:22 | 162 | 900.07
2024/4/2 | 11:54:39 | 163 | 914.77
2024/4/2 | 11:54:55 | 164 | 924.76
2024/4/2 | 11:55:11 | 165 | 937.93
2024/4/2 | 11:55:27 | 166 | 950.49
2024/4/2 | 11:55:43 | 167 | 965.61
2024/4/2 | 11:55:59 | 168 | 977.31
2024/4/2 | 11:56:16 | 169 | 984.23
2024/4/2 | 11:56:32 | 170 | 1004.19
2024/4/2 | 11:56:48 | 171 | 1021.14
2024/4/2 | 11:57:4 | 172 | 1033.03
2024/4/2 | 11:57:21 | 173 | 1044.58
2024/4/2 | 11:57:42 | 174 | 1051.96
2024/4/2 | 11:57:58 | 175 | 1070.15
2024/4/2 | 11:58:14 | 176 | 1085.64
2024/4/2 | 11:58:30 | 177 | 1107.52
2024/4/2 | 11:58:46 | 178 | 1125.35
2024/4/2 | 11:59:2 | 179 | 1141.51
2024/4/2 | 11:59:18 | 180 | 1158.39
2024/4/2 | 11:59:34 | 181 | 1175.16
2024/4/2 | 11:59:50 | 182 | 1190.67
2024/4/2 | 12:0:6 | 183 | 1206.28
2024/4/2 | 12:0:22 | 184 | 1222.22
2024/4/2 | 12:0:38 | 185 | 1238.13
2024/4/2 | 12:0:54 | 186 | 1253.92
2024/4/2 | 12:1:10 | 187 | 1266.90
2024/4/2 | 12:1:26 | 188 | 1282.32
2024/4/2 | 12:1:42 | 189 | 1295.46
2024/4/2 | 12:1:58 | 190 | 1309.33
2024/4/2 | 12:2:14 | 191 | 1324.48
2024/4/2 | 12:2:30 | 192 | 1339.84
2024/4/2 | 12:2:47 | 193 | 1354.50
2024/4/2 | 12:3:4 | 194 | 1366.20
2024/4/2 | 12:3:21 | 195 | 1368.98
2024/4/2 | 12:3:37 | 196 | 1362.39
2024/4/2 | 12:3:53 | 197 | 1395.71
2024/4/2 | 12:4:9 | 198 | 1414.67
2024/4/2 | 12:4:25 | 199 | 1430.64
2024/4/2 | 12:4:41 | 200 | 1445.00
2024/4/2 | 12:4:58 | 201 | 1458.74
2024/4/2 | 12:5:14 | 202 | 1471.67
2024/4/2 | 12:5:30 | 203 | 1485.66
2024/4/2 | 12:5:46 | 204 | 1501.66
2024/4/2 | 12:6:2 | 205 | 1516.53
2024/4/2 | 12:6:18 | 206 | 1531.96
2024/4/2 | 12:6:34 | 207 | 1547.41
2024/4/2 | 12:6:50 | 208 | 1562.68
2024/4/2 | 12:7:6 | 209 | 1576.61
2024/4/2 | 12:7:22 | 210 | 1591.82
2024/4/2 | 12:7:38 | 211 | 1608.19
2024/4/2 | 12:7:54 | 212 | 1623.27
2024/4/2 | 12:8:10 | 213 | 1637.96
2024/4/2 | 12:8:26 | 214 | 1653.81
2024/4/2 | 12:8:42 | 215 | 1669.30
2024/4/2 | 12:8:58 | 216 | 1681.61
2024/4/2 | 12:9:14 | 217 | 1696.58
2024/4/2 | 12:9:30 | 218 | 1708.98
2024/4/2 | 12:9:46 | 219 | 1727.79
2024/4/2 | 12:10:2 | 220 | 1741.66
2024/4/2 | 12:10:18 | 221 | 1757.54
2024/4/2 | 12:10:34 | 222 | 1772.53
2024/4/2 | 12:10:50 | 223 | 1786.28
2024/4/2 | 12:11:6 | 224 | 1800.00
2024/4/2 | 12:11:22 | 225 | 1813.44
2024/4/2 | 12:11:38 | 226 | 1827.55
2024/4/2 | 12:11:55 | 227 | 1841.45
2024/4/2 | 12:12:11 | 228 | 1854.22
2024/4/2 | 12:12:29 | 229 | 1870.86
2024/4/2 | 12:12:46 | 230 | 1885.19
2024/4/2 | 12:13:2 | 231 | 1899.57
2024/4/2 | 12:13:18 | 232 | 1914.17
2024/4/2 | 12:13:34 | 233 | 1928.93
2024/4/2 | 12:13:50 | 234 | 1943.01
2024/4/2 | 12:14:6 | 235 | 1957.06
2024/4/2 | 12:14:22 | 236 | 1970.32
2024/4/2 | 12:14:38 | 237 | 1984.92
2024/4/2 | 12:14:54 | 238 | 2000.22
2024/4/2 | 12:15:10 | 239 | 2017.99
2024/4/2 | 12:15:26 | 240 | 2037.83
2024/4/2 | 12:15:42 | 241 | 2057.67
2024/4/2 | 12:15:58 | 242 | 2079.10
2024/4/2 | 12:16:14 | 243 | 2098.09
2024/4/2 | 12:16:31 | 244 | 2118.51
2024/4/2 | 12:16:47 | 245 | 2138.39
2024/4/2 | 12:17:3 | 246 | 2161.46
2024/4/2 | 12:17:19 | 247 | 2184.96
2024/4/2 | 12:17:40 | 248 | 2213.27
2024/4/2 | 12:17:59 | 249 | 2237.11
2024/4/2 | 12:18:16 | 250 | 2257.23
2024/4/2 | 12:18:32 | 251 | 2282.62
2024/4/2 | 12:18:49 | 252 | 2309.16
2024/4/2 | 12:19:6 | 253 | 2335.38
2024/4/2 | 12:19:23 | 254 | 2361.56
2024/4/2 | 12:19:39 | 255 | 2385.61
2024/4/2 | 12:19:56 | 256 | 2409.66
2024/4/2 | 12:20:12 | 257 | 2431.79
2024/4/2 | 12:20:28 | 258 | 2455.93
2024/4/2 | 12:20:44 | 259 | 2482.23
2024/4/2 | 12:21:0 | 260 | 2507.44
2024/4/2 | 12:21:16 | 261 | 2530.54
2024/4/2 | 12:21:33 | 262 | 2555.93
2024/4/2 | 12:21:49 | 263 | 2582.48
2024/4/2 | 12:22:5 | 264 | 2612.59
2024/4/2 | 12:22:21 | 265 | 2640.27
2024/4/2 | 12:22:37 | 266 | 2664.84
2024/4/2 | 12:22:54 | 267 | 2692.45
2024/4/2 | 12:23:10 | 268 | 2716.83
2024/4/2 | 12:23:27 | 269 | 2738.41
2024/4/2 | 12:23:43 | 270 | 2760.76
2024/4/2 | 12:23:59 | 271 | 2783.28
2024/4/2 | 12:24:17 | 272 | 2808.18
2024/4/2 | 12:24:33 | 273 | 2829.73
2024/4/2 | 12:24:49 | 274 | 2849.39
2024/4/2 | 12:25:5 | 275 | 2864.36
2024/4/2 | 12:25:21 | 276 | 2882.71
2024/4/2 | 12:25:37 | 277 | 2900.14
2024/4/2 | 12:25:53 | 278 | 2921.20
2024/4/2 | 12:26:9 | 279 | 2945.07
2024/4/2 | 12:26:25 | 280 | 2963.54
2024/4/2 | 12:26:41 | 281 | 2985.09
2024/4/2 | 12:26:57 | 282 | 3004.81
2024/4/2 | 12:27:13 | 283 | 3024.38
2024/4/2 | 12:27:29 | 284 | 3049.46
2024/4/2 | 12:27:45 | 285 | 3075.10
2024/4/2 | 12:28:2 | 286 | 3097.59
2024/4/2 | 12:28:26 | 287 | 3128.80
2024/4/2 | 12:28:45 | 288 | 3153.40
2024/4/2 | 12:29:2 | 289 | 3179.06
2024/4/2 | 12:29:19 | 290 | 3202.32
2024/4/2 | 12:29:36 | 291 | 3225.06
2024/4/2 | 12:29:52 | 292 | 3250.02
2024/4/2 | 12:30:8 | 293 | 3275.41
2024/4/2 | 12:30:24 | 294 | 3300.92
2024/4/2 | 12:30:40 | 295 | 3325.61
2024/4/2 | 12:30:56 | 296 | 3349.51
2024/4/2 | 12:31:12 | 297 | 3373.50
2024/4/2 | 12:31:28 | 298 | 3398.58
2024/4/2 | 12:31:48 | 299 | 3422.78
2024/4/2 | 12:32:5 | 300 | 3445.40
2024/4/2 | 12:32:38 | 301 | 3480.42
2024/4/2 | 12:32:54 | 302 | 3520.87
2024/4/2 | 12:33:10 | 303 | 3547.63
2024/4/2 | 12:33:26 | 304 | 3571.89
2024/4/2 | 12:33:43 | 305 | 3596.12
2024/4/2 | 12:34:0 | 306 | 3617.55
2024/4/2 | 12:34:16 | 307 | 3641.72
2024/4/2 | 12:34:32 | 308 | 3669.88
2024/4/2 | 12:35:26 | 309 | 3687.99
2024/4/2 | 12:36:15 | 310 | 3687.29
2024/4/2 | 12:39:17 | 311 | 3681.95
2024/4/2 | 12:54:20 | 312 | 3686.53
2024/4/2 | 12:54:48 | 313 | 3687.35
2024/4/2 | 12:59:53 | 314 | 3686.65
2024/4/2 | 13:33:53 | 315 | 3672.99
2024/4/2 | 13:34:48 | 316 | 3672.57
2024/4/2 | 13:35:5 | 317 | 3644.83
2024/4/2 | 13:36:38 | 318 | 3629.83
2024/4/2 | 13:36:55 | 319 | 3616.67
2024/4/2 | 13:37:12 | 320 | 3598.47
2024/4/2 | 13:37:28 | 321 | 3602.10
2024/4/2 | 13:37:44 | 322 | 3598.26
2024/4/2 | 13:39:39 | 323 | 3605.66
2024/4/2 | 13:40:31 | 324 | 3607.31
2024/4/2 | 13:40:48 | 325 | 3598.74
2024/4/2 | 13:41:4 | 326 | 3594.20
2024/4/2 | 13:41:21 | 327 | 3589.63
2024/4/2 | 13:41:50 | 328 | 3585.58
2024/4/2 | 13:42:26 | 329 | 3586.76
2024/4/2 | 13:42:43 | 330 | 3581.70
2024/4/2 | 13:43:0 | 331 | 3597.98
2024/4/2 | 13:43:16 | 332 | 3617.49
2024/4/2 | 13:43:38 | 333 | 3617.46
2024/4/2 | 13:43:54 | 334 | 3619.93
2024/4/2 | 13:44:10 | 335 | 3619.99
2024/4/2 | 13:44:26 | 336 | 3620.72
2024/4/2 | 13:44:42 | 337 | 3618.10
2024/4/2 | 13:44:58 | 338 | 3624.68
2024/4/2 | 13:45:14 | 339 | 3632.30
2024/4/2 | 13:45:30 | 340 | 3635.17
2024/4/2 | 13:45:46 | 341 | 3636.75
2024/4/2 | 13:46:2 | 342 | 3637.64
2024/4/2 | 13:46:18 | 343 | 3640.77
2024/4/2 | 13:46:34 | 344 | 3643.46
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

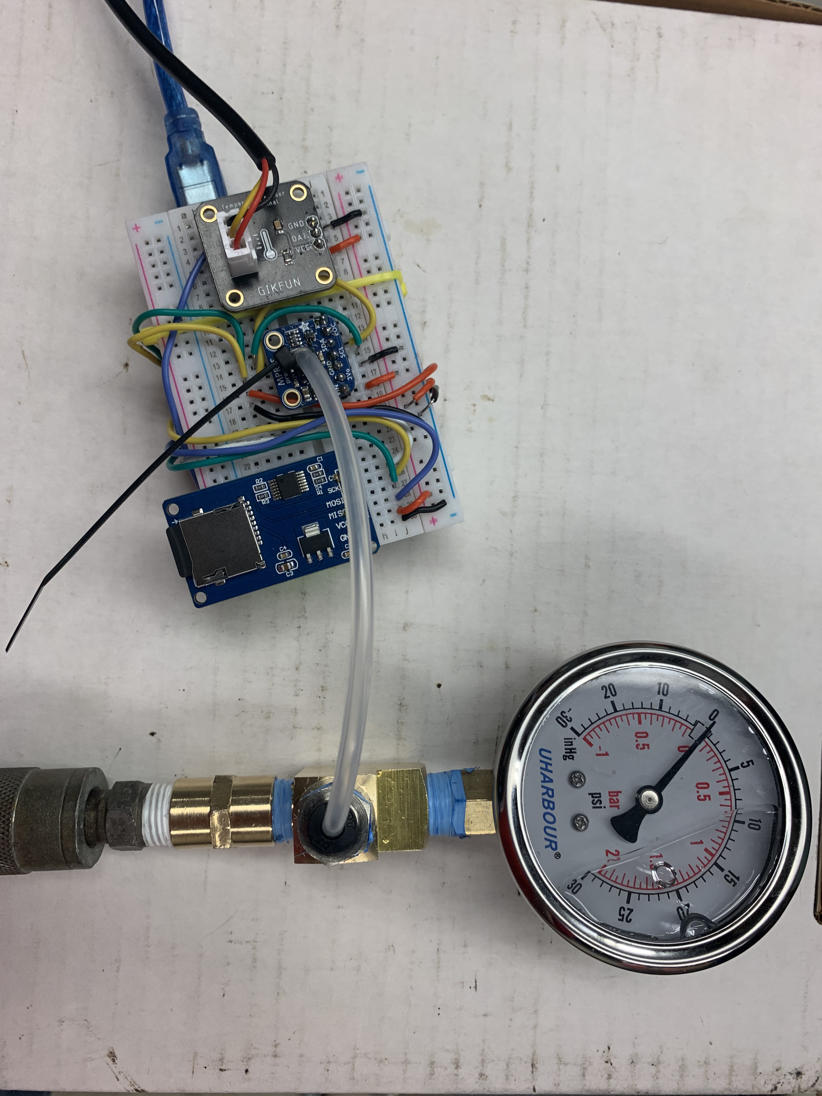
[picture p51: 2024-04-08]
Reference-Photos/Pressure-Sensor-Validation-Test-Apparatus.jpeg

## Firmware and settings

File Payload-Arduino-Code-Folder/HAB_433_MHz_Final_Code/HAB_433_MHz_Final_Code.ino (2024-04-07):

//--------------------------------------------------------------------------------------------------------------
// These are all the libraries that need to be loaded in for this code to run
//--------------------------------------------------------------------------------------------------------------

#include <OneWire.h>            // This is for the temperature sensors
#include <DallasTemperature.h>  // This is for the temperature sensors
#include <SPI.h>                // This is to communicate with SPI devices (In this case: Pressure Sensor, Temperature Sensor, Radio Module)
#include <Adafruit_MPRLS.h>     // This is for the pressure sensor
#include <Wire.h>               // This is for the pressure sensor
#include <SD.h>                 // This is for saving backup data to the SD card
#include <Arduino_MKRGPS.h>     // This is for the GPS shield
#include <LoRa.h>               // This is for the MKR WAN 1310 board / Radio Module
#include <RTClib.h>             // This is for the Real Time Clock board

//--------------------------------------------------------------------------------------------------------------
// This is for the temperature sensors
//--------------------------------------------------------------------------------------------------------------

// This is to define what pins each temp. sensor data wire is connected to (Should be a digital pin)
#define ONE_WIRE_BUS 7  // All temperature sensors connected to pin# 1

// This is to define the precision of the temperature sensors
#define TEMPERATURE_PRECISION 12  // Sets the OneWire precision Dallas Sensor (12 bits = 0.0625°C)

// This is to pass OneWire references to Dallas Temperature library
OneWire oneWire(ONE_WIRE_BUS);        // Pull OneWire Reference
DallasTemperature sensors(&oneWire);  // Transfer OneWire reference to Dallas Temperature

// This is denoting which temperature sensor is interior/exterior.
// To get their addresses, rune the "BLANK CODE" in order to determine which address is what sensor
DeviceAddress InsideThermometer = { 0x28, 0x6F, 0x5E, 0x58, 0xD4, 0xE1, 0x3C, 0x21 };
DeviceAddress OutsideThermometer = { 0x28, 0x91, 0x82, 0x58, 0xD4, 0xE1, 0x3C, 0x3F };

//--------------------------------------------------------------------------------------------------------------
// This is for the pressure sensor
//--------------------------------------------------------------------------------------------------------------

// This is to define the pins for Reset and EOC (End of Conversation). This isn't using them so we will define those to the Arduino reset pin
#define RESET_PIN -1  // Connected to Arduino reset pin (pin# -1). Change to anything else if you desire
#define EOC_PIN -1    // Connected to Arduino reset pin (pin# -1). Change to anything else if you desire
Adafruit_MPRLS mpr = Adafruit_MPRLS(RESET_PIN, EOC_PIN);

//--------------------------------------------------------------------------------------------------------------
// This is for the camera and SD card
//--------------------------------------------------------------------------------------------------------------

// Define the pins for the camera and SD card
#define SD_PIN 1               // This is the pin that the CS leg of thecamera is connected to
#define Trigger_PIN 0           // This is the pin that tells the camera to take a photo
int photoNumber = 0;            // This keeps track of the photo number

// This creates a File object to store the file
File BackUpData;
File PhotoData;

// Define timers to photos
const int Picture_Interval_MS = 15000;   // This is the timer for taking pictures
int Next_Picture_At = millis() + 5000;

//--------------------------------------------------------------------------------------------------------------
// This is for the LoRa Module on the Arduino MKR WAN 1310
//--------------------------------------------------------------------------------------------------------------

// Counter to keep track of every packet of information
int counter = 0;

//--------------------------------------------------------------------------------------------------------------
// This is for the RTC chip (Real Time Clock)
//--------------------------------------------------------------------------------------------------------------

// Initialzes the rtc chip
RTC_PCF8523 rtc;

void setup() {
  //----------------------------------------------------------------------------------------------------------------
  // This is all the setup code that gets ran only once (upon startup)
  //----------------------------------------------------------------------------------------------------------------
  Serial.begin(115200);
  while (!Serial) {
    ;  // This waits for the serial port to connect
  }

  //--------------------------------------------------------------------------------------------------------------
  // This is for setting up the trigger pin for the camera
  //--------------------------------------------------------------------------------------------------------------
  pinMode(Trigger_PIN, OUTPUT);
  digitalWrite(Trigger_PIN, LOW);

  //--------------------------------------------------------------------------------------------------------------
  // This is for the temperature sensors
  //--------------------------------------------------------------------------------------------------------------

  // Starts up library / sensors
  sensors.begin();  // This starts everything up
  Serial.println("Intializing temperature sensors...");
  delay(1000);
  if (sensors.getDeviceCount() == 0) {
    Serial.println("Failed to initialize temperature sensor");
  } else Serial.println("Temperature sensors ready!");
  delay(1000);       // 1 second delay to give everything FLAIR
  Serial.println();  // Insert space

  //--------------------------------------------------------------------------------------------------------------
  // This is to set the precision of both temperature sensor
  //--------------------------------------------------------------------------------------------------------------

  sensors.setResolution(InsideThermometer, TEMPERATURE_PRECISION);
  sensors.setResolution(OutsideThermometer, TEMPERATURE_PRECISION);

  //--------------------------------------------------------------------------------------------------------------
  // This is for the pressure sensor
  //--------------------------------------------------------------------------------------------------------------

  // Starts up library
  Serial.println("Initializing pressure sensor...");
  delay(1000);  // 1 second delay to give everything FLAIR
  if (!mpr.begin()) {
    Serial.println("Failed to initialize pressure sensor!");
  } else Serial.println("Pressure sensor ready!");
  delay(1000);       // 1 second delay to give everything FLAIR
  Serial.println();  // Insert space

  //--------------------------------------------------------------------------------------------------------------
  // This is for the MKR GPS Shield
  //--------------------------------------------------------------------------------------------------------------

  // This is to initialize the GPS Shield
  Serial.println("Initializing GPS Shield...");
  delay(1000);  // 1 second delay to give everything FLAIR
  if (!GPS.begin(GPS_MODE_SHIELD)) {
    Serial.println("Failed to initialize GPS!");
    while (1)
      ;
  } else Serial.println("GPS Ready!");
  delay(1000);       // 1 second delay to give everything FLAIR
  Serial.println();  // Insert space

  //--------------------------------------------------------------------------------------------------------------
  // This is for the SD card board
  //--------------------------------------------------------------------------------------------------------------

  // This initializes the SD Card
  Serial.println("Initializing MKR WAN 1310 SD Card...");
  delay(1000);  // 1 second delay to give everything FLAIR
  if (!SD.begin(SD_PIN)) {
    Serial.println("Failed to initialize MKR WAN 1310 SD card!");
    while(1) delay(1);   // This waits for an SD card to be insertted
  } else Serial.println("MKR WAN 1310 SD card ready!");
  delay(1000);       // 1 second delay to give everything FLAIR
  Serial.println();  // Insert space

  //--------------------------------------------------------------------------------------------------------------
  // This is for the Real Time Clock board
  //--------------------------------------------------------------------------------------------------------------

  Serial.println("Initializing RTC Board...");
  delay(1000);  // 1 second delay to give everything FLAIR

  // This locates the RTC board
  if (! rtc.begin()) {
    Serial.println("Couldn't find RTC");
    Serial.flush();
    while (1) delay(10);  // This holds up the entire code until it can find the RTC board
  }

  rtc.start();
  
  rtc.adjust(DateTime(F(__DATE__), F(__TIME__)));

  //--------------------------------------------------------------------------------------------------------------
  // This is for setting up the .csv file that will act as the backup incase radio malfunction
  //--------------------------------------------------------------------------------------------------------------

  // This will get the current date fpr the file name
  DateTime now = rtc.now();
  Serial.println("Today's Date is:");
  Serial.println(String(now.day(), DEC) + "/" + String(now.month(), DEC) + "/" + String(now.year(), DEC));
  String fileName = "HAB_Flight_" + String(now.day(), DEC) + String(now.month(), DEC) + String(now.year(), DEC) + ".csv";
  delay(1000);  // 1 second delay to give everything FLAIR
  Serial.println();  // Insert space

  // Write header to SD card
  // NOTE: The .csv filename can be a MAXIUMUM of 8 characters long. Otherwise, it just doesn't create the file. Something to do with memory restrictions
  Serial.println("Setting up .csv Data Files on SD Card...");
  delay(1000);  // 1 second delay to give everything FLAIR
  
  SD.remove("HAB_Test.csv");
  SD.remove("PhotoDat.csv");

  File BackUpData = SD.open("HAB_Test.csv", FILE_WRITE);

  if (BackUpData) {
    BackUpData.println("Date(YYYY-MM-DD),Timestamp(HH:MM:SS),Interior_Temperature_(\xB0""F),Exterior_Temperature_(\xB0""F),Pressure_(psi),Latitude(\xB0""),Longitude(\xB0""),Altitude(ft),#_of_Satellites"); // The \xB0"" prints a degree symbol
    BackUpData.close();
    Serial.println(".csv backup file created!");
    BackUpData.close();
  } else {
    Serial.println("Error constructing .csv backup file!");
  }
  delay(1000);  // 1 second delay to give everything FLAIR

  File PhotoData = SD.open("PhotoDat.csv", FILE_WRITE);

  if (PhotoData) {
    PhotoData.println("Date(YYYY-MM-DD),Timestamp(HH:MM:SS),Photo_Number,GPS_Altitude(ft)"); // The \xB0"" prints a degree symbol
    PhotoData.close();
    Serial.println(".csv photo data file created!");
    PhotoData.close();
  } else {
    Serial.println("Error constructing .csv photo file!");
  }
  delay(1000);  // 1 second delay to give everything FLAIR
  Serial.println();  // Insert space


  //--------------------------------------------------------------------------------------------------------------
  // This is for setting up the LoRa radio transmitter
  //--------------------------------------------------------------------------------------------------------------
  
  Serial.println("Initializing LoRa Module...");
  delay(1000);  // 1 second delay to give everything FLAIR

  // This is for 433 MHz Signal (Australian Radio Frequency 915 MHz)
  
    // This sets up the LoRa radio
    if (!LoRa.begin(433E6)) {
      Serial.println("Starting LoRa failed!");
      while (1);
    }

    // This sets up some special parameters for this application in order to boost the signal of the radio (Hopefully)
    LoRa.setTxPower(20);
    LoRa.setSpreadingFactor(11);
    LoRa.setSignalBandwidth(62.5E3);
    LoRa.crc();  

  // This sends the heading information for the .csv file that the reciever should be creating

    //// This is if we are sending ALL the data. Comment out if we just want the GPS data
    //LoRa.beginPacket();
    //LoRa.print("Packet,Date(YYY-MM-DD),Timestamp(HH:MM:SS),Interior_Temperature_(\xB0""F),Exterior_Temperature_(\xB0""F),Pressure_(psi),Latitude(\xB0""),Longitude(\xB0""),Altitude(ft),#_of_Satellites");
    //LoRa.endPacket();

    //// This is if we are sending JUST the GPS data. Comment out if we are sending ALL the data.
    //LoRa.beginPacket();
    //LoRa.print("Packet,Latitude(°),Longitude(°),Altitude(ft)");
    //LoRa.endPacket();

  //--------------------------------------------------------------------------------------------------------------
  // This is for printing all data to serial monitor (Comment out probably just to save computing power)
  //--------------------------------------------------------------------------------------------------------------

  Serial.println();  // Insert space
  Serial.println("START DATA...");
  Serial.println();  // Insert space
  delay(1000);       // 1 second delay to give everything FLAIR
  Serial.println("|----------------|-------------------------|-------------------------|-------------------|-----------------|------------------|------------------|-----------------|");
  Serial.println("|    Timer(s) \t |   Int_Temperature(°F)   |   Ext_Temperature(°F)   |   Pressure(psi)   |   Latitude(°)   |   Longitude(°)   |   Altitude(ft)   | # of Satellites |");
  Serial.println("|----------------|-------------------------|-------------------------|-------------------|-----------------|------------------|------------------|-----------------|");

  delay(1);  // Delay to get column labels down correctly

}

void loop() {
  //----------------------------------------------------------------------------------------------------------------
  // This is the part of the code that runs continuously
  // This loop deals with gathering and printing sensor and location data and sending it back to "base"
  // Note: This is only going to run if GPS data is available!
  //----------------------------------------------------------------------------------------------------------------

   if (GPS.available()) {

    //--------------------------------------------------------------------------------------------------------------
    // This for the GPS Shield / reads the current GPS values
    //--------------------------------------------------------------------------------------------------------------
    float Current_Latitude = GPS.latitude();    // Degrees
    float Current_Longitude = GPS.longitude();  // Degrees
    float Current_Altitude = GPS.altitude();    // Meters
    float Current_Speed = GPS.speed();          // Kilometers/Hour
    float Satellites = GPS.satellites();          // Just number of satellites pinging to GPS

    //--------------------------------------------------------------------------------------------------------------
    // This is for the temperature sensors / reads current temperatures
    //--------------------------------------------------------------------------------------------------------------
    sensors.requestTemperatures();

    //--------------------------------------------------------------------------------------------------------------
    // This is for the pressure sensor / reads current pressure
    //--------------------------------------------------------------------------------------------------------------
    mpr.readPressure();

    //--------------------------------------------------------------------------------------------------------------
    // This is for the RTC chip / reads current date and time
    //--------------------------------------------------------------------------------------------------------------
    DateTime now = rtc.now();

    //----------------------------------------------------------------------------------------------------------------
    // This is for printing all data to the backup .csv file on the SD card
    //----------------------------------------------------------------------------------------------------------------

    //String fileName = "HAB_Flight_" + String(now.day(), DEC) + String(now.month(), DEC) + String(now.year(), DEC) + ".csv";
    File BackUpData = SD.open("HAB_Test.csv", FILE_WRITE);

    if (BackUpData) {
      BackUpData.print(String(now.year(), DEC) + "/" + String(now.month(), DEC) + "/" + String(now.day(), DEC));
      BackUpData.print(",");
      BackUpData.print(String(now.hour(), DEC) + ":" + String(now.minute(), DEC) + ":" + String(now.second(), DEC));
      BackUpData.print(",");
      BackUpData.print(sensors.getTempF(InsideThermometer));
      BackUpData.print(",");
      BackUpData.print(sensors.getTempF(OutsideThermometer));
      BackUpData.print(",");
      BackUpData.print(mpr.readPressure() / 68.947572932);
      BackUpData.print(",");
      BackUpData.print(Current_Latitude, 7);
      BackUpData.print(",");
      BackUpData.print(Current_Longitude, 7);
      BackUpData.print(",");
      BackUpData.print(Current_Altitude / 3.280839895);
      BackUpData.print(",");
      BackUpData.println(Satellites);
      BackUpData.close();
    } else {
      Serial.println("Error Opening Backup Data File...");
    }

    //----------------------------------------------------------------------------------------------------------------
    // This is for printing all data to the serial monitor for lab testing
    // Note: Can and probably should comment this out before actually launching balloon
    //----------------------------------------------------------------------------------------------------------------

    Serial.print("|\t");
    Serial.print(millis() / 1000);
    Serial.print("\t |     \t");
    Serial.print(" ");
    Serial.print(" ");
    Serial.print(" ");
    Serial.print(" ");
    Serial.print(sensors.getTempF(InsideThermometer));  // Fahrenheit
    Serial.print("          | \t ");
    Serial.print(" ");
    Serial.print(" ");
    Serial.print(" ");
    Serial.print(" ");
    Serial.print(" ");
    Serial.print(sensors.getTempF(OutsideThermometer));  // Fahrenheit
    Serial.print("          | \t ");
    Serial.print(" ");
    Serial.print(" ");
    Serial.print(" ");
    Serial.print(" ");
    Serial.print(mpr.readPressure() / 68.947572932);  // psi
    Serial.print("       | ");
    Serial.print(" ");
    Serial.print(" ");
    Serial.print(" ");
    Serial.print(Current_Latitude, 7);  // Degrees
    Serial.print("   | ");
    Serial.print(" ");
    Serial.print(" ");
    Serial.print(" ");
    Serial.print(Current_Longitude, 7);  // Degrees
    Serial.print("   | ");
    Serial.print(" ");
    Serial.print(" ");
    Serial.print(" ");
    Serial.print(" ");
    Serial.print(" ");
    Serial.print(Current_Altitude / 3.280839895);  // ft
    Serial.print("       | \t ");
    Serial.print(" ");
    Serial.print(Satellites);  // Amount
    Serial.print("        | ");

    Serial.println();  // Begin new line

    //----------------------------------------------------------------------------------------------------------------
    // This is for sending data via LoRa
    //----------------------------------------------------------------------------------------------------------------

      // This sends ALL the data. Comment out if just want GPS position
      LoRa.beginPacket();
      LoRa.print("BLAW426");
      LoRa.print(",");
      LoRa.print("Packet ");
      LoRa.print(counter);
      LoRa.print(",");
      LoRa.print(String(now.year(), DEC) + "/" + String(now.month(), DEC) + "/" + String(now.day(), DEC));
      LoRa.print(",");
      LoRa.print(String(now.hour(), DEC) + ":" + String(now.minute(), DEC) + ":" + String(now.second(), DEC));
      LoRa.print(",");
      LoRa.print(sensors.getTempF(InsideThermometer));
      LoRa.print(",");
      LoRa.print(sensors.getTempF(OutsideThermometer));
      LoRa.print(",");
      LoRa.print(mpr.readPressure() / 68.947572932);
      LoRa.print(",");
      LoRa.print(Current_Latitude, 7);
      LoRa.print(",");
      LoRa.print(Current_Longitude, 7);
      LoRa.print(",");
      LoRa.print(Current_Altitude / 3.280839895);
      LoRa.print(",");
      LoRa.print(Satellites);
      LoRa.endPacket();

      //// This sends JUST the GPS data. Comment out if want ALL the data.
      //LoRa.beginPacket();
      //LoRa.print("Packet ");
      //LoRa.print(counter);
      //LoRa.print(",");
      //LoRa.print(Current_Latitude, 7);
      //LoRa.print(",");
      //LoRa.print(Current_Longitude, 7);
      //LoRa.print(",");
      //LoRa.print(Current_Altitude / 3.280839895);
      //LoRa.endPacket();

    // This increases tha packet counter up 1
    counter++;

    //----------------------------------------------------------------------------------------------------------------
    // This is for telling the camera its time to take a picture
    //----------------------------------------------------------------------------------------------------------------

    if(millis() > Next_Picture_At){
      Serial.println("Sent Photo Request...");

      File PhotoData = SD.open("PhotoDat.csv", FILE_WRITE);

      if (PhotoData) {

      PhotoData.print(String(now.year(), DEC) + "/" + String(now.month(), DEC) + "/" + String(now.day(), DEC));
      PhotoData.print(",");
      PhotoData.print(String(now.hour(), DEC) + ":" + String(now.minute(), DEC) + ":" + String(now.second(), DEC));
      PhotoData.print(",");
      PhotoData.print(String(photoNumber));
      PhotoData.print(",");
      PhotoData.println(Current_Altitude / 3.280839895);
      PhotoData.close();
      }
      else {
        Serial.println("Error Opening Backup Data File...");
      }

      digitalWrite(Trigger_PIN, HIGH);
      delay(100);
      digitalWrite(Trigger_PIN, LOW);

      Next_Picture_At = millis() + Picture_Interval_MS;

      ++photoNumber;
      

    }
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

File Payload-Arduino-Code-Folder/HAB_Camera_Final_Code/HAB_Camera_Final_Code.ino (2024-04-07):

#include "esp_camera.h"         // Library for Camera/ESP32-CAM Board
#include "Arduino.h"            // Library for Arduino
#include "SD_MMC.h"             // Library for microSD Card
#include "FS.h"                 // Library for microSD Card
#include "soc/soc.h"            // Disable brownout problems
#include "soc/rtc_cntl_reg.h"   // Disable brownout problems
  
#define CAMERA_MODEL_AI_THINKER // Has PSRAM

// Pin definition for CAMERA_MODEL_AI_THINKER
#define PWDN_GPIO_NUM     32
#define RESET_GPIO_NUM    -1
#define XCLK_GPIO_NUM      0
#define SIOD_GPIO_NUM     26
#define SIOC_GPIO_NUM     27

#define Y9_GPIO_NUM       35
#define Y8_GPIO_NUM       34
#define Y7_GPIO_NUM       39
#define Y6_GPIO_NUM       36
#define Y5_GPIO_NUM       21
#define Y4_GPIO_NUM       19
#define Y3_GPIO_NUM       18
#define Y2_GPIO_NUM        5
#define VSYNC_GPIO_NUM    25
#define HREF_GPIO_NUM     23
#define PCLK_GPIO_NUM     22

// Define Trigger Pin
#define Trigger_PIN       1

const char * photoPrefix = "/Photo_";
int photoNumber = 0;

void setup() {
  Serial.begin(115200);
  while (!Serial) {
    ;  // This waits for the serial port to connect
  }
  Serial.setDebugOutput(true);
  Serial.println();

  camera_config_t config;
  config.ledc_channel = LEDC_CHANNEL_0;
  config.ledc_timer = LEDC_TIMER_0;
  config.pin_d0 = Y2_GPIO_NUM;
  config.pin_d1 = Y3_GPIO_NUM;
  config.pin_d2 = Y4_GPIO_NUM;
  config.pin_d3 = Y5_GPIO_NUM;
  config.pin_d4 = Y6_GPIO_NUM;
  config.pin_d5 = Y7_GPIO_NUM;
  config.pin_d6 = Y8_GPIO_NUM;
  config.pin_d7 = Y9_GPIO_NUM;
  config.pin_xclk = XCLK_GPIO_NUM;
  config.pin_pclk = PCLK_GPIO_NUM;
  config.pin_vsync = VSYNC_GPIO_NUM;
  config.pin_href = HREF_GPIO_NUM;
  config.pin_sscb_sda = SIOD_GPIO_NUM;
  config.pin_sscb_scl = SIOC_GPIO_NUM;
  config.pin_pwdn = PWDN_GPIO_NUM;
  config.pin_reset = RESET_GPIO_NUM;
  config.xclk_freq_hz = 20000000;
  config.pixel_format = PIXFORMAT_JPEG;

  if (psramFound()) {
    config.frame_size = FRAMESIZE_UXGA;
    config.jpeg_quality = 15;
    config.fb_count = 2;
  } else {
    config.frame_size = FRAMESIZE_UXGA;
    config.jpeg_quality = 15;
    config.fb_count = 2;
  }

  #if defined(CAMERA_MODEL_ESP_EYE)
  pinMode(13, INPUT_PULLUP);
  pinMode(14, INPUT_PULLUP);
  #endif

  // camera init
  esp_err_t err = esp_camera_init( & config);
  if (err != ESP_OK) {
    Serial.printf("Camera init failed with error 0x%x", err);
    return;
  }

  sensor_t * s = esp_camera_sensor_get();
  // initial sensors are flipped vertically and colors are a bit saturated
  if (s -> id.PID == OV3660_PID) {
    s -> set_vflip(s, 1); // flip it back
    s -> set_brightness(s, 1); // up the brightness just a bit
    s -> set_saturation(s, -2); // lower the saturation
  }
  // drop down frame size for higher initial frame rate
  s -> set_framesize(s, FRAMESIZE_UXGA);

  #if defined(CAMERA_MODEL_M5STACK_WIDE) || defined(CAMERA_MODEL_M5STACK_ESP32CAM)
  s -> set_vflip(s, 1);
  s -> set_hmirror(s, 1);
  #endif

  Serial.println("Initialising Camera SD card");
  if (!SD_MMC.begin()) {
    Serial.println("Failed to initialise Camea SD card!");
    return;
  }

  uint8_t cardType = SD_MMC.cardType();
  if (cardType == CARD_NONE) {
    Serial.println("Camera SD card slot appears to be empty!");
    return;
  }

  pinMode(Trigger_PIN, INPUT);

}

void loop() {

  if (digitalRead(Trigger_PIN) == HIGH) {

    Capture_and_Save_Photo();

  }

  delay(100);
  
}

void Capture_and_Save_Photo() {

  camera_fb_t * fb = NULL;
  fb = esp_camera_fb_get();
  if (!fb) {
    Serial.println("Camera capture failed");
    return;
  }

  String photoFileName = photoPrefix + String(photoNumber) + ".jpg";
  fs::FS & fs = SD_MMC;
  Serial.printf("Picture file name: %s\n", photoFileName.c_str());

  File file = fs.open(photoFileName.c_str(), FILE_WRITE);
  if (!file) {
    Serial.println("Failed to open file in writing mode");
  } else {
    file.write(fb -> buf, fb -> len);
    Serial.printf("Saved file to path: %s\n", photoFileName.c_str());
    ++photoNumber;
  }
  file.close();
  esp_camera_fb_return(fb);

}
